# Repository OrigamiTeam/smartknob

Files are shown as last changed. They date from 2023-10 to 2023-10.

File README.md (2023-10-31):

# ⚠️⚠️⚠️ IBOM is not updated for my variant of the PCB, don't order blindly ⚠️⚠️⚠️

# SmartKnob
SmartKnob is an open-source input device with software-configurable endstops and virtual detents.

A brushless gimbal motor is paired with a magnetic encoder to provide closed-loop torque feedback control, making it
possible to dynamically create and adjust the feel of detents and endstops.

Join the [Discord community](https://discord.gg/5jyhjcbTnR) to discuss the project with others, show off your build, or help answer each others' questions!




# Designs

## SmartKnob View
The "SmartKnob View" is the premium SmartKnob experience with an integrated display shown in my [demo video](https://www.youtube.com/watch?v=ip641WmY4pA). Under active development.

🎉 **Motors are [now available](https://www.sparkfun.com/products/20441)!** If you've been following this project,
you'll know that the recommended motors went out of stock nearly immediately after it was published.
Thanks to [the community](https://github.com/scottbez1/smartknob/issues/16#issuecomment-1094482805%5D), we were able to
identify the likely original manufacturer, and recently SparkFun Electronics has been getting them produced and regularly
[stocking them](https://www.sparkfun.com/products/20441)! (However, they've been selling out quickly each time they restock, so definitely sign up for backorder notifications if they're out of stock when you check). Thanks to everyone who helped search and investigate different
motor options along the way!

Features:
 - 240x240 round LCD ("GC9A01"), protected by 39.5mm watch glass on rotor
 - BLDC gimbal motor, with a hollow shaft for mechanically & electrically connecting the LCD
 - Powered by ESP32-PICO-V3-02 (Lilygo TMicro32 Plus module)
 - PCB flexure and SMD resistors used as strain gauges for press detection (haptic feedback provided via the motor)
 - 8 side-firing RGB LEDs (SK6812-SIDE-A) illuminate ring around the knob
 - USB-C (2.0) connector for 5V power and serial data/programming (CH340)
 - VEML7700 ambient light sensor for automatic backlight & LED intensity adjustment
 - Versatile back plate for mounting - use either 4x screws, or 2x 3M medium Command strips (with cutouts for accessing removal tabs after installation)
 - Front cover snaps on for easy access to the PCB

**Current status:** Not recommended for general use, but may be a fun project for an advanced electronics hobbyist.

### Demo video

<a href="https://www.youtube.com/watch?v=ip641WmY4pA">
    
</a>

### How it works
<a href="https://www.youtube.com/watch?v=Q76dMggUH1M">
    
</a>

### 3D CAD

Exploded view

Latest Fusion 360 Model: https://a360.co/3BzkU0n

### Build your own?

While this is a "DIY" open-source project, it is not yet a mature plug-and-play project. If you intend to build your own, note that it requires advanced soldering experience to build - very small-pitch surface-mount soldering is required (reflow or hot air recommended), and assembly is quite time-consuming and delicate. Please go into it with the expectation that you will almost certainly need to be able to troubleshoot some hardware and firmware issues yourself - I recommend reviewing/understanding the schematics and basic firmware before jumping in!

More documentation on the BOM and what parts you need to order is coming in the future - thanks so much for your interest! Follow me on [Twitter](https://twitter.com/scottbez1) for the latest updates on this and other projects.

View the latest auto-generated (untested) [Base PCB Interactive BOM](https://smartknob-artifacts.s3.us-west-1.amazonaws.com/master/electronics/view_base-ibom.html) and [Screen PCB Interactive BOM](https://smartknob-artifacts.s3.us-west-1.amazonaws.com/master/electronics/view_screen-ibom.html) (or, the combined [BOM csv](https://smartknob-artifacts.s3.us-west-1.amazonaws.com/master/electronics/view_base-bom.csv)) for electronics/hardware parts list. ⚠️ These are auto-generated from the latest untested revision on GitHub. For tested/stable/recommended artifacts, use a [release](https://github.com/scottbez1/smartknob/releases) instead.

A few miscellaneous notes in the meantime:

 - There's limited space inside the LCD mount for wiring, and 8 wires need to fit through the hole in the center. I used 30 AWG wire-wrapping wire. Enamel-coated wire would probably work too.
 - Older versions of the design (as seen in the videos) used glued-on BF350-3AA strain gauges to detect presses; in v0.5 these were replaced with footprints for SMD resistors, which exhibit similar properties when stretched/compressed and are much easier to assemble. 
 - The TMC6300 is _tiny_ and has a bottom pad, so I would seriously consider getting a stencil along with the PCB order. Even with the stencil I needed to manually clean up some bridging afterward; I _highly_ recommend Chip Quik NC191 gel flux, available on [Amazon](https://amzn.to/3MGDSr5) (or use this [non-affiliate link](https://www.amazon.com/Smooth-Flow-No-Clean-syringe-plunger/dp/B08KJPG3NZ) instead) or from your electronics distributor of choice. Flux is also very helpful when soldering the LCD ribbon cable to to screen PCB.
 - For breadboard prototyping, the [TMC6300-BOB](https://www.trinamic.com/support/eval-kits/details/tmc6300-bob/) or SparkFun's [TMC6300 driver board](https://www.sparkfun.com/products/21867) are awesome and way easier to work with than the bare chip if you just want to play around with low current BLDC motors
 - For AliExpress purchases: I highly recommend **only** using AliExpress Standard Shipping (purchasing in the US). I have had multiple purchases take months or never get delivered when purchased with Cainiao or other low cost shipping options, whereas AliExpress Standard is very reliable and generally faster in my experience.
 - Make sure to check the [open issues](https://github.com/scottbez1/smartknob/issues) - this design is not yet "stable", so beware that everything may not go smoothly.

Future plans:
 - consider switch to using an ESP32-S3-MINI-1 module
 - get wifi configured and working (probably MQTT?). Currently memory is an issue with the full display framebuffer sprite. PSRAM might fix this (requires newer ESP-IDF & unreleased Arduino core, and from a brief test I got horrible performance with PSRAM enabled), or the next item might help reduce memory:
 - migrate to LVGL, for better display rendering and easy support for menus, etc. Shouldn't require a full 240x240x24b framebuffer in memory, freeing some for wifi, etc.
 - Home Assistant integration, or other real-world applications
 - ???
 - [Profit](https://github.com/sponsors/scottbez1/) 😉

 #### Already built one?
Check out the [firmware/software documentation](https://paper.dropbox.com/doc/SmartKnob-firmware-and-software--B_oWj~L1dXqHgAqqYmhwwuqzAg-VUb9nq7btuhnHw5KlgJIH)
for tips on getting it programmed and hooking it up to your own software integrations.

If you've already uploaded the standard firmware and gone through the calibration process (see guide linked above if you don't know what this means),
go to https://scottbez1.github.io/smartknob/ to try out an interactive web-based demo that uses Web Serial to talk to a SmartKnob that's plugged into your
computer's USB port!

#### Base PCB

<a href="https://smartknob-artifacts.s3.us-west-1.amazonaws.com/master/electronics/view_base-front-3d.png">
    
</a>
<a href="https://smartknob-artifacts.s3.us-west-1.amazonaws.com/master/electronics/view_base-back-3d.png">
    
</a>

Ordering notes: use white soldermask, for reflecting light from RGB LED ring around the knob. Should be 1.2mm thick (not "standard" 1.6mm).

If you are ordering a stencil for solder paste from JLCPCB and plan to apply paste by hand (as
[shown in the video](https://youtu.be/Q76dMggUH1M?t=372)) without a stencil frame/machine, make sure to select
**"Customized size"** and enter smaller dimensions (e.g. 100mm x 100mm) to avoid getting a much larger stencil than you
need. This will also likely reduce the cost of shipping substantially! Also, select only the **Top** side; the bottom
only has 2 SMT components - the motor connector and VEML7700 ALS - so it's not worth getting a stencil for that.

Latest auto-generated (untested and likely broken!) artifacts⚠️:

[Schematic](https://smartknob-artifacts.s3.us-west-1.amazonaws.com/master/electronics/view_base-schematic.pdf)

[Interactive BOM](https://smartknob-artifacts.s3.us-west-1.amazonaws.com/master/electronics/view_base-ibom.html)

[PCB Packet](https://smartknob-artifacts.s3.us-west-1.amazonaws.com/master/electronics/view_base-pcb-packet.pdf)

[Gerbers](https://smartknob-artifacts.s3.us-west-1.amazonaws.com/master/electronics/view_base-jlc/gerbers.zip)

⚠️ For tested/stable/recommended artifacts, use a [release](https://github.com/scottbez1/smartknob/releases) instead.

#### Screen PCB

<a href="https://smartknob-artifacts.s3.us-west-1.amazonaws.com/master/electronics/view_screen-front-3d.png">
    
</a>
<a href="https://smartknob-artifacts.s3.us-west-1.amazonaws.com/master/electronics/view_screen-back-3d.png">
    
</a>

Ordering notes: Must be 1.2mm thick (not "standard" 1.6mm) per mechanical design. (The PCB silkscreen mentions 0.6mm thickness - this is the thickness of the **VHB tape** for adhering the LCD; the PCB should be 1.2mm thick)

There are few enough components on the Screen PCB that I chose to hand-solder them rather than reflow with solder paste
and a stencil, but if you order a stencil, see the note above about selecting a "Customized size" to be easier to
handle and save on shipping. Also make sure to select the **Bottom** side only; all the components are on the bottom
side of the screen PCB.

Latest auto-generated (untested and likely broken!) artifacts⚠️:

[Schematic](https://smartknob-artifacts.s3.us-west-1.amazonaws.com/master/electronics/view_screen-schematic.pdf)

[Interactive BOM](https://smartknob-artifacts.s3.us-west-1.amazonaws.com/master/electronics/view_screen-ibom.html)

[PCB Packet](https://smartknob-artifacts.s3.us-west-1.amazonaws.com/master/electronics/view_screen-pcb-packet.pdf)

[Gerbers](https://smartknob-artifacts.s3.us-west-1.amazonaws.com/master/electronics/view_screen-jlc/gerbers.zip)

⚠️ For tested/stable/recommended artifacts, use a [release](https://github.com/scottbez1/smartknob/releases) instead.

#### Printed parts
You will need six printed parts. The current stable designs can be found as STL assets in the [v185 mechanical release](https://github.com/scottbez1/smartknob/releases/tag/releases%2Fmechanical%2Fv185-dummy-tag) or you can export the latest untested designs from the CAD model by opening it in Fusion 360: https://a360.co/3BzkU0n

The parts can _probably_ be FDM 3D printed with a well-tuned printer, but the parts shown in videos/photos were MJF printed in nylon for tight tolerances and better surface finish. 

If you wanted a simpler build, you could omit the LCD and just merge the knob + glass from the model into a single STL to get a closed-top knob.

Export and print the following 6 parts:
* `Enclosure`
* `Knob` (RotorAssembly->KnobAssembly->Knob)
* `ScreenPlatform`
* `RotorSpacer` (RotorAssembly->RotorSpacer)
* `MountBase`
* `BackPlate`

⚠️ If you opt to go for MJF Nylon printing from JLCPCB, their system may complain about `< 0.8mm wall thickness detected` on the `MountBase`, `ScreenPlatform` and `RotorSpacer` parts. This appears to be a false positive, possibly on some of the print tapers. You should be able to ignore this, as all print orders at JLCPCB are subject to a final manual review, and they will contact you by email if there are any job-stopping issues or risks with your prints.

## NanoFOC (3rd party)
If you're looking to tinker with FOC/haptic feedback, but don't want to build a full SmartKnob View yourself, I can
recommend the NanoFOC DevKit++, an [open-source design](https://github.com/katbinaris/nanofoc_devkit) made and
[sold](https://store.binaris.io/products/nanofoc-devkit) by a member of the SmartKnob community! It's super compact
and is a great testbed or core for building your own BLDC-based haptic input device.

Image of the NanoFOC PCB

The NanoFOC uses an ESP32-S3, and the SmartKnob firmware works on it out of the box; just select the `nanofoc`
environment in PlatformIO rather than the `view` environment when uploading.

# Frequently Asked Questions (FAQ)

### Can I use this cheap gimbal BLDC motor I found on AliExpress?

I can't stop you, but I will caution that **you probably won't be super happy with it** depending on your intended application.

Nearly every off-the-shelf BLDC gimbal motor that the community has tested (which is pretty much ALL the cheap ones you'll find on AliExpress, trust me) has
_moderate to severge cogging_. That means the motor wants to snap to certain positions by itself even when unpowered. This means you won't be able to get
completely smooth rotation when virtual detents are turned off, and the motor's cogging may interfere with or overpower the virtual detents, particularly if
you set them to lower strength or make then very fine-grained.

The recommended motor is definitely the best (i.e. lowest cogging) off-the-shelf motor we've come across so far, and is the only readily-available motor
that I would consider "good" for this application.

If you've found another motor that is completely smooth when unpowered, we'd LOVE to hear about it in the discord; if you're wondering about some cheap motor
you saw online, either just order one and try it for yourself, or ask about it in discord but don't be surprised (or offended) if the response you get is
something terse like "nope, no good".

### How much does it cost?

I wish I could tell you now, but I don't actually know off the top of my head. Check back soon - I've only built a few so far, which was the result of a bunch of tinkering and prototyping over an extended period, so I don't have all the expenses tallied up yet. Probably less than $200 in parts? But some items have gotten more expensive, and you may be limited by minimum order quantities or shipping charges from multiple separate suppliers.

### Does it work with XYZ?

Not yet, regardless of whatever "XYZ" you're thinking of. So far I've only implemented enough firmware for the demo shown in the video, so you can't actually use it for anything productive yet. The basic detent configuration API is there, but not much else. Lots of firmware work remains to be done. If you build one, I'd love your help adding support for "XYZ" though!

### Can I buy one as a kit or already assembled?

Probably not? Or at least, I don't have any immediate plans to sell them myself. It's not that I don't want you to be happy, but hardware is a hard business and I just work on this stuff in my free time.

It's open source with a fairly permissive license though, so in theory anyone could start offering kits/assemblies. If someone does go down that route of selling them, note that attribution is
 _required_ (and I wouldn't say no to [royalties/tips/thanks](https://github.com/sponsors/scottbez1/) if you're in a giving mood 🙂).

# Firmware and Software
More extensive documentation of the firmware and software (and how to get started) can be found in the dedicated [SmartKnob Firmware and Software Guide](https://paper.dropbox.com/doc/SmartKnob-firmware-and-software--Byho6npe9XvZLZLxJ_8bK5TqAg-VUb9nq7btuhnHw5KlgJIH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)

## General Component Info

### Magnetic encoders

#### MT6701 (MagnTek)
Excellent sensor at a reasonable price - highly recommended. Less noisy than TLV493D, and more responsive (control loop is more stable) using SSI.

 - Lots of IO options - SSI, I2C, and ABZ - should offer good response latency
 - SSI includes CRC to validate data
 - No power-down or low-power options - may not be ideal for battery-powered devices
 - Not available from US distributors (Mouser, Digi-Key)

[Datasheet](http://www.magntek.com.cn/upload/MT6701_Rev.1.5.pdf)

[Ordering (LCSC)](https://lcsc.com/product-detail/Angle-Linear-Position-Sensors_Magn-Tek-MT6701CT-STD_C2856764.html)

#### TLV493D (Infineon)
Not used in the SmartKnob view, but a common/popular magnetic encoder in general. It's a mediocre choice for a haptic feedback implementation. Easy to prototype with using [Adafruit's QWIIC breakout board](https://www.adafruit.com/product/4366).

In my testing, it's noisy, requiring filtering/smoothing that can slow responsiveness, hurting control loop stability. Or, with less filtering, the noise
can easily be "amplified" by the derivative component in the PID motor torque controller, causing audible (and tactile) humming/buzzing.

But the bigger issue is that there is apparently a known silicon issue that causes the internal ADC to sometimes completely lock up, requiring a full reset and re-configuration, which can cause delays/gaps in data! See section
5.6 in the [User Manual](https://www.infineon.com/dgdl/Infineon-TLV493D-A1B6_3DMagnetic-UM-v01_03-EN.pdf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)

    In the Master Controlled Mode (MCM) or the Fast Mode (FM) the ADC conversion may hang up. A hang up can
    be detected by:
     - Frame Counter (FRM) counter stucks and does not increment anymore.

In my experience testing 4 different Adafruit breakout boards, 2 of them (50%) regularly exhibit this lockup behavior within a minute or two of use. It is possible to detect and auto-reset (and there is code in the project to do so), but it is slow and may cause undesirable jumps/delays if the sensor locks up often.

[Datasheet](https://www.mouser.com/datasheet/2/196/Infineon_TLV493D_A1B6_DataSheet_v01_10_EN-1227967.pdf)

#### AS5600 (AMS)
A mediocre choice. Cheap breakout boards are readily available.

In my testing, it's fairly noisy (anecdotally, noisier than the TLV493d), requiring filtering/smoothing that can slow responsiveness, hurting control loop stability. Additionally, it saturates at a lower magnetic field strength than other sensors I tested, requiring a significant air gap (8-10mm) when used with a strong neodymium diametric magnet like [Radial Magnets 8995](https://www.digikey.com/en/products/detail/radial-magnets-inc/8995/5126077).

[Datasheet](https://ams.com/documents/20143/36005/AS5600_DS000365_5-00.pdf)

### Motor drivers
#### TMC6300-LA
This is a relatively new IC and it's a perfect match! There generally aren't any other drivers (with integrated fets) that meet the requirements for the low-voltage and low-current motors used in this project (DRV8316 might work, but has not been tested).

Highlights:
 - 2-11V DC motor supply input
 - Up to 1.2A RMS
 - Tiny (3x3mm QFN)

 [Datasheet](https://www.trinamic.com/fileadmin/assets/Products/ICs_Documents/TMC6300_datasheet_rev1.07.pdf)

 [Product page](https://www.trinamic.com/products/integrated-circuits/details/tmc6300-la/)

### Motors
#### 32mm Rotor, Hollow Shaft, Diametric magnet



- 32mm rotor
- 15mm overall height (including magnet), 12.75mm height w/o magnet, 9mm rotor height
- low/zero cogging - excellent for completely smooth input
- 5.9mm hollow shaft
- built-in diametric magnet for encoder
- Proven option

This is overall the easiest motor to get started with. Low cogging and a built-in diametric magnet are great!

Available [from SparkFun](https://www.sparkfun.com/products/20441)!

# Acknowledgements
This project was greatly inspired by Jesse Schoch's video "[haptic textures and virtual detents](https://www.youtube.com/watch?v=1gPQfDkX3BU)" and the
corresponding [discussion in the SimpleFOC community](https://community.simplefoc.com/t/haptic-textures/301). Seriously, this project wouldn't exist if not for that video - thank you Jesse!

# License

This project is licensed under Apache v2 (software, electronics, documentation) and Creative Commons Attribution 4.0 (hardware/mechanical) (see [LICENSE.txt](LICENSE.txt) and [Creative Commons](https://creativecommons.org/licenses/by/4.0/)).

    Copyright 2022 Scott Bezek
    
    Licensed under the Apache License, Version 2.0 (the "License");
    you may not use this file except in compliance with the License.
    You may obtain a copy of the License at
    
        http://www.apache.org/licenses/LICENSE-2.0
    
    Unless required by applicable law or agreed to in writing, software
    distributed under the License is distributed on an "AS IS" BASIS,
    WITHOUT WARRANTIES OR CONDITIONS OF ANY KIND, either express or implied.
    See the License for the specific language governing permissions and
    limitations under the License.

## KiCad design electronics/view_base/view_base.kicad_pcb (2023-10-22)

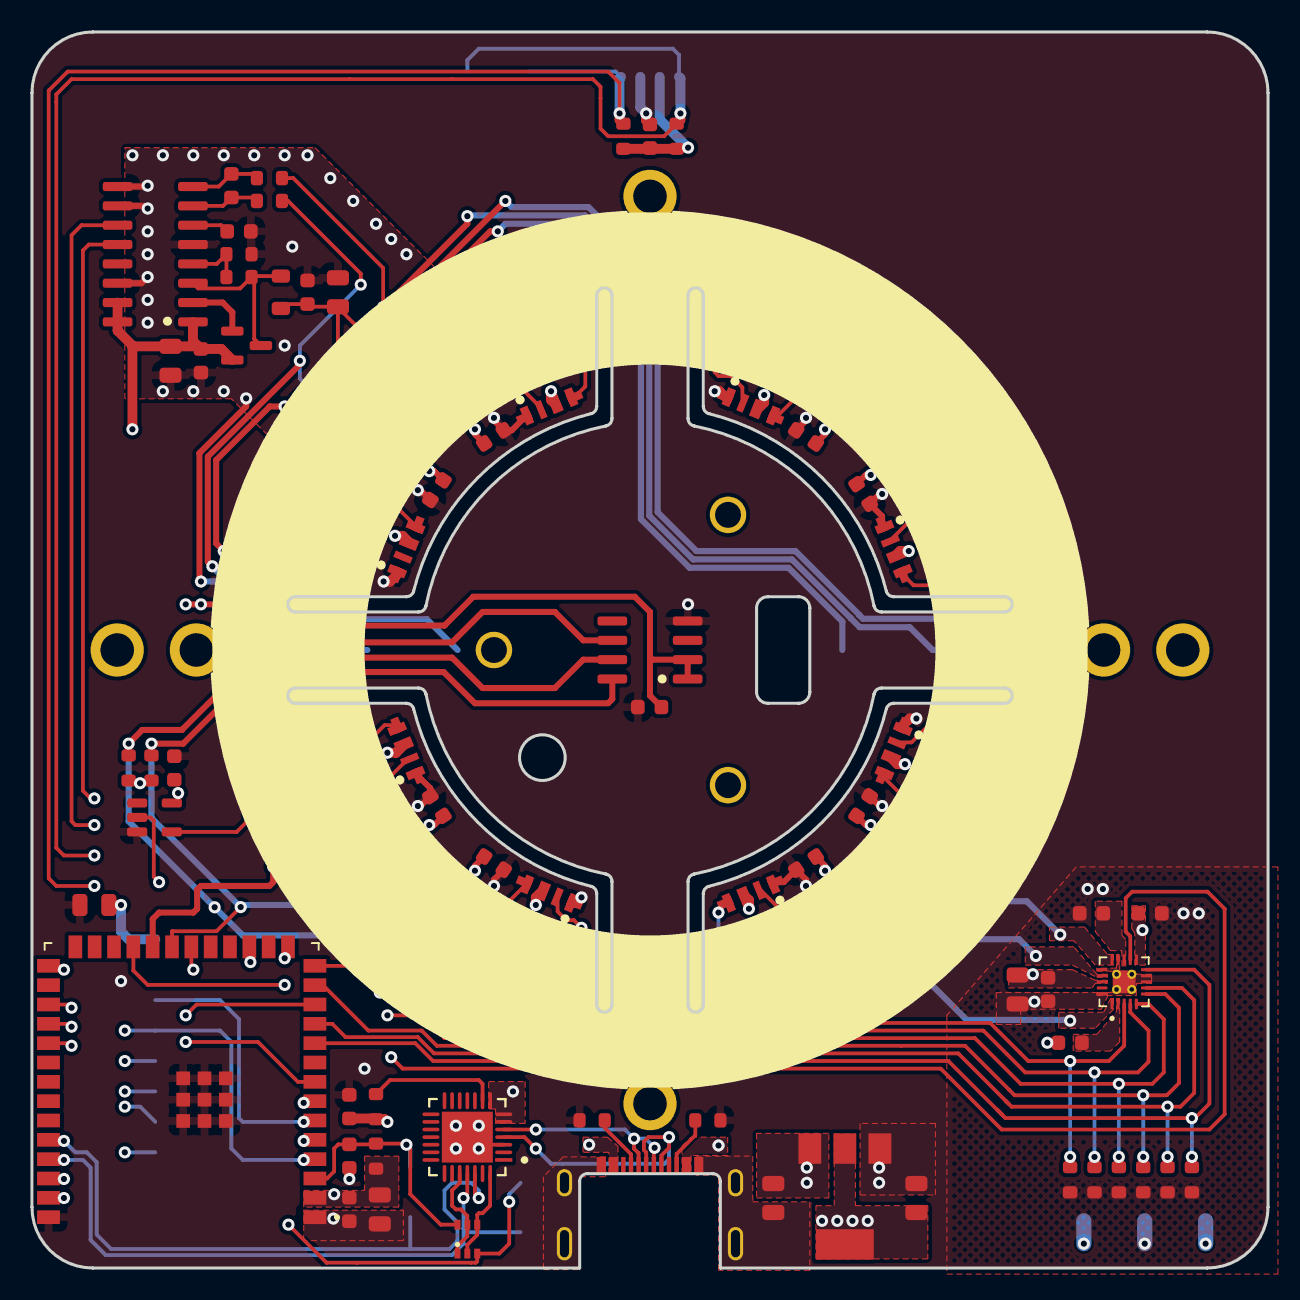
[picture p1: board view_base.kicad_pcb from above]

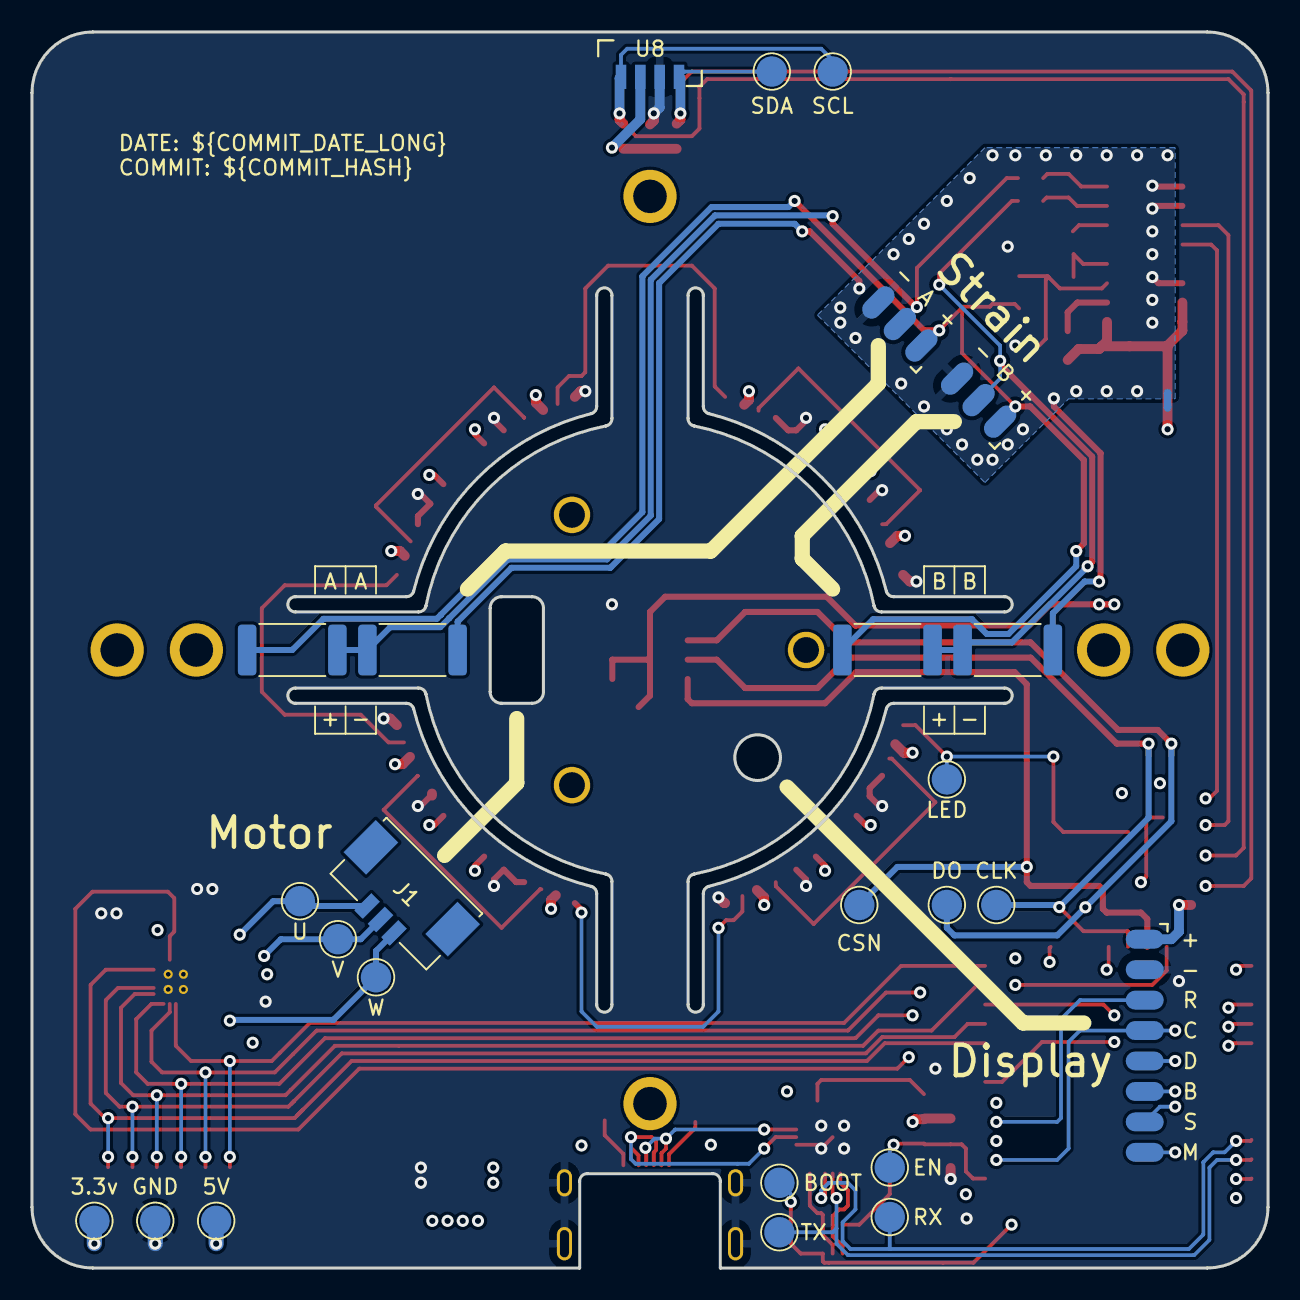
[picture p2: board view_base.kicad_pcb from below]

Board: 4 copper layers, 81.2 x 81.2 mm, 107 parts (26 on the bottom side), 58 nets.

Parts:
C1, C2, C3, C4, C5, C6, C7, C8, C11, C12, C14, C15, C17, C19, C20, C21, C22, C23, C25, C27, C29: 0.1uF; C_0603_1608Metric
C9, C10, C16, C18, C24, C26: 10uF; C_0805_2012Metric
C13: 22uF; C_0805_2012Metric
C28: 1uF; C_0603_1608Metric
D1, D2, D3, D4, D5, D6, D7, D8: SK6812SIDE-A; SK6812-SIDE-A
H1, H2, H3: MotorHole; MountingHole_M1.6
H4, H5, H6, H7: MountHole; MountingHole_2.2mm_M2_ISO7380_Pad_NonVirtual
H8, H9: AlignmentHole; MountingHole_2.2mm_M2_ISO7380_Pad_NonVirtual
J1: BLDC; 532610371
J2: USB_C_Receptacle_USB2.0; USB4510_NoPaste
J3: LCD; SolderPads_2mm_8
J4: A; SolderPads_2mm_3_STRAIN
J5: B; SolderPads_2mm_3_STRAIN
L1: 3.3uH; L_0805_2012Metric
NT1: NetTie_2; NetTie-2_SMD_Pad0.5mm
Q1: MMBT4403; SOT-23
Q2: UMH3N; SOT-363_SC-70-6
R1, R2: 5.1k; R_0603_1608Metric
R3, R7, R8, R9, R10, R11, R12, R17: 10k; R_0603_1608Metric
R4: 8.2k; R_0603_1608Metric
R5, R6: 100; R_0603_1608Metric
R13, R14, R15, R16: 2.2k; R_0603_1608Metric
R18, R19, R20, R21: 330; R_2512_6332Metric
R22: 1K; R_0603_1608Metric
TP1: 5V; TestPoint_Pad_D2.0mm_ValueSilk
TP2: 3.3v; TestPoint_Pad_D2.0mm_ValueSilk
TP3: GND; TestPoint_Pad_D2.0mm_ValueSilk
TP4: SDA; TestPoint_Pad_D2.0mm_ValueSilk
TP5: SCL; TestPoint_Pad_D2.0mm_ValueSilk
TP6: U; TestPoint_Pad_D2.0mm_ValueSilk
TP7: V; TestPoint_Pad_D2.0mm_ValueSilk
TP8: W; TestPoint_Pad_D2.0mm_ValueSilk
TP9: CSN; TestPoint_Pad_D2.0mm_ValueSilk
TP10: CLK; TestPoint_Pad_D2.0mm_ValueSilk
TP11: DO; TestPoint_Pad_D2.0mm_ValueSilk
TP12: LED; TestPoint_Pad_D2.0mm_ValueSilk
TP13: EN; TestPoint_Pad_D2.0mm_ValueSilk
TP14: BOOT; TestPoint_Pad_D2.0mm_ValueSilk
TP15: TX; TestPoint_Pad_D2.0mm_ValueSilk
TP16: RX; TestPoint_Pad_D2.0mm_ValueSilk
U1: MT6701-CT; SOIC-8_3.9x4.9mm_P1.27mm
U2: CP2102N-A02-GQFN28; Silicon_Labs-CP2102N-A02-GQFN28-IPC_A
U4: HX711; SOIC-16_3.9x9.9mm_P1.27mm
U5: TMC6300; QFN-20-1EP_3x3mm_P0.4mm_EP1.65x1.65mm_ThermalVias_LargerVia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
U7: SN74LV1T34DBV; SOT-23-5
U8: VEML7700; VEML7700-TOP
U9: TS1117BCW33_RPG; SOT-223-3_TabPin2_GndOutIn
U10: ESP32-S3-WROOM-1-N8R8; XCVR_ESP32S3WROOM1N8R8U
Z5: dummy_keepouts; ViewKeepouts3d
Z6, Z7, Z8: RotorScrew (BOM-only); bom_only_no_pin
Z9: WatchGlass39.5mm; bom_only_no_pin
Z10: BLDCMotor; bom_only_no_pin

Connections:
+3V3: C10.1, C11.1, C12.1, C16.1, C17.1, C20.1, C24.1, C25.1, C26.1, C27.1, J3.1, Q1.2 (E), R13.1, R14.1, R15.1, R16.2, R17.1, R22.1, TP2.1, U1.1 (VDD), U1.2 (MODE), U2.6 (VDD), U2.7 (VREGIN), U2.8 (VBUS), U4.1 (VSUP), U4.15 (RATE), U4.16 (DVDD), U5.11 (VIO/~STDBY), U8.2 (VDD), U9.2 (Output), U10.2 (3V3)
+5V: C1.1, C2.1, C3.1, C4.1, C5.1, C6.1, C7.1, C8.1, C9.1, C13.1, C14.1, C15.1, C29.1, D1.2 (VDD), D2.2 (VDD), D3.2 (VDD), D4.2 (VDD), D5.2 (VDD), D6.2 (VDD), D7.2 (VDD), D8.2 (VDD), J2.A4 (VBUS), J2.A9 (VBUS), J2.B4 (VBUS), J2.B9 (VBUS), TP1.1, U5.18 (VS), U7.5 (VCC), U9.3 (Input)
/DTR: Q2.2 (B1), Q2.4 (E2), U2.28 (DTR)
/ESP32_BOOT: Q2.3 (C2), TP14.1, U10.27 (IO0)
/ESP32_EN: C28.1, Q2.6 (C1), R17.2, TP13.1, U10.3 (EN)
/LCD_BACKLIGHT: J3.6, U10.5 (IO5)
/LCD_CMD: J3.8, U10.38 (IO2)
/LCD_CS: J3.7, U10.17 (IO9)
/LCD_DATA: J3.5, U10.15 (IO3)
/LCD_RST: J3.3, U10.6 (IO6)
/LCD_SCK: J3.4, U10.4 (IO4)
/LED_DATA_3V3: U7.2 (A), U10.7 (IO7)
/LED_DATA_5V: D1.1 (DIN), TP12.1, U7.4 (Y)
/MAG_CLK: R16.1, TP10.1, U1.7 (B/V/SCL/CLK), U10.21 (IO13)
/MAG_CSN: TP9.1, U1.8 (Z/W/CSN), U10.22 (IO14)
/MAG_DO: R15.2, TP11.1, U1.6 (A/U/SDA/DO), U10.30 (IO37)
/RTS: Q2.1 (E1), Q2.5 (B2), U2.24 (RTS)
/SCL: R14.2, TP5.1, U8.1 (SCL), U10.12 (IO8)
/SDA: R13.2, TP4.1, U8.4 (SDA), U10.8 (IO15)
/STRAIN_DO: U4.12 (DOUT), U10.31 (IO38)
/STRAIN_E+: C18.1, C19.1, J4.1, J5.1, L1.2, R18.1, R20.2
/STRAIN_S+: J4.2, R6.1, R18.2, R19.1
/STRAIN_S-: J5.2, R5.2, R20.1, R21.2
/STRAIN_SCK: U4.11 (PD_SCK), U10.39 (IO1)
/TMC_DIAG: U5.12 (DIAG), U10.29 (IO36)
/TMC_UH: R7.1, U5.3 (UH), U10.14 (IO20)
/TMC_UL: R10.1, U5.6 (UL), U10.13 (IO19)
/TMC_VH: R8.1, U5.4 (VH), U10.23 (IO21)
/TMC_VL: R12.1, U5.10 (VL), U10.10 (IO17)
/TMC_WH: R9.1, U5.5 (WH), U10.20 (IO12)
/TMC_WL: R11.1, U5.7 (WL), U10.11 (IO18)
/USB_CC1: J2.A5 (CC1), R1.1
/USB_CC2: J2.B5 (CC2), R2.1
/USB_D+: J2.A6 (D+), J2.B6 (D+), U2.4 (D+)
/USB_D-: J2.A7 (D-), J2.B7 (D-), U2.5 (D-)
/USB_SERIAL_RXI: TP15.1, U2.25 (RXD), U10.37 (TXD0)
/USB_SERIAL_TXO: TP16.1, U2.26 (TXD), U10.36 (RXD0)
GND: C1.2, C2.2, C3.2, C4.2, C5.2, C6.2, C7.2, C8.2, C9.2, C10.2, C11.2, C13.2, C14.2, C17.2, C20.2, C21.2, C24.2, C25.2, C26.2, C27.2, C28.2, C29.2, D1.4 (VSS), D2.4 (VSS), D3.4 (VSS), D4.4 (VSS), D5.4 (VSS), D6.4 (VSS), D7.4 (VSS), D8.4 (VSS), J2.A1 (GND), J2.A12 (GND), J2.B1 (GND), J2.B12 (GND), J2.S1 (SHIELD), J3.2, NT1.2, R1.2, R2.2, R7.2, R8.2, R9.2, R10.2, R11.2, R12.2, TP3.1, U1.4 (GND), U2.3 (GND), U2.29 (GND), U5.8 (GND), U5.9 (GND), U5.14 (GND), U5.16 (BRUV), U5.20 (BRW), U5.PAD, U7.3 (GND), U8.3 (GND), U9.1 (GND), U10.1 (GND), U10.40 (GND), U10.41_1 (GND), U10.41_2 (GND), U10.41_3 (GND), U10.41_4 (GND), U10.41_5 (GND), U10.41_6 (GND), U10.41_7 (GND), U10.41_8 (GND), U10.41_9 (GND)
GNDA: C12.2, C16.2, C18.2, C19.2, C22.1, J4.3, J5.3, NT1.1, R4.2, R19.2, R21.1, U4.5 (AGND), U4.9 (INB-), U4.10 (INB+), U4.14 (XI)
unnamed: D1.3 (DOUT), D2.1 (DIN)
unnamed: D2.3 (DOUT), D3.1 (DIN)
unnamed: D3.3 (DOUT), D4.1 (DIN)
unnamed: D4.3 (DOUT), D5.1 (DIN)
unnamed: D5.3 (DOUT), D6.1 (DIN)
unnamed: D6.3 (DOUT), D7.1 (DIN)
unnamed: D7.3 (DOUT), D8.1 (DIN)
unnamed: J1.1, TP8.1, U5.1 (W)
unnamed: J1.2, TP7.1, U5.17 (V)
unnamed: J1.3, TP6.1, U5.15 (U)
unnamed: Q1.1 (B), U4.2 (BASE)
unnamed: L1.1, Q1.3 (C), R3.1, U4.3 (AVDD)
unnamed: R22.2, U2.9 (~RST)
unnamed: C23.1, R6.2, U4.8 (INA+)
unnamed: C23.2, R5.1, U4.7 (INA-)
unnamed: C22.2, U4.6 (VBG)
unnamed: R3.2, R4.1, U4.4 (VFB)
unnamed: C21.1, U5.13 (1V8OUT)
unnamed: C15.2, U5.2 (VCP)

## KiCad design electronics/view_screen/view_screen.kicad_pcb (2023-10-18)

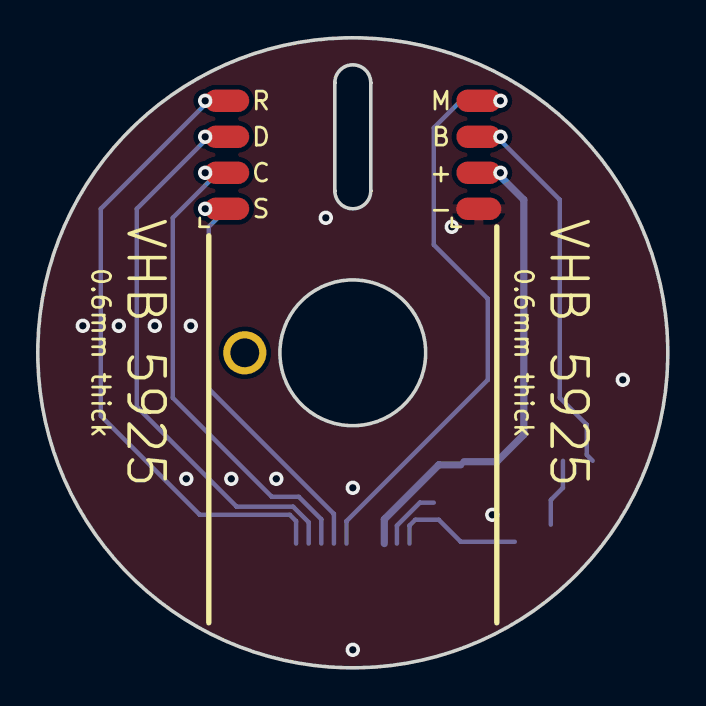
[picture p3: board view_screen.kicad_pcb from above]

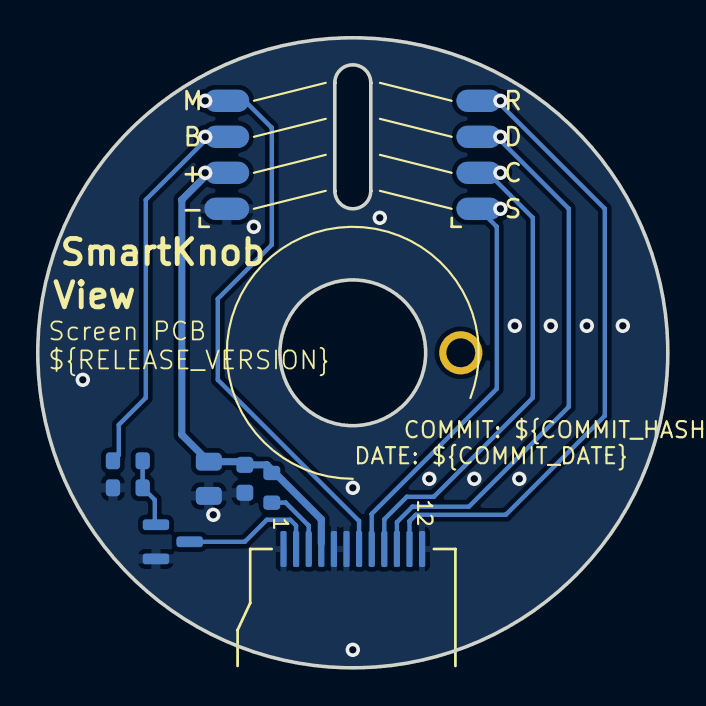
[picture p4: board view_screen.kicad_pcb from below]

Board: 2 copper layers, 35.0 x 35.0 mm, 12 parts (9 on the bottom side), 11 nets.

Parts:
C1: 22uF; C_0805_2012Metric
C2: 0.1uF; C_0603_1608Metric
H1: AlignmentHole; AlignmentHole_1.6
J1, J3, J4, J5: Conn_01x04; SolderPads_2mm_4
J2: GC9A01; GC9A01Round1.28
Q1: 2N7002; SOT-23
R1: 10k; R_0603_1608Metric
R2: 22R; R_0603_1608Metric
R3: 1M; R_0603_1608Metric

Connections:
/BACKLIGHT_EN: J1.3, J4.3, R1.1
/DC: J1.4, J2.7, J4.4
/LEDA: J2.3, R2.2
/LEDK: J2.2, Q1.3 (D)
/MOSI: J2.10, J3.3, J5.3
/SCK: J2.9, J3.2, J5.2
/VDD: C1.1, C2.1, J1.2, J2.4, J4.2, R2.1
/nCS: J2.8, J3.1, J5.1
/nRESET: J2.11, J3.4, J5.4
GND: C1.2, C2.2, J1.1, J2.1, J2.5, J2.6, J2.12, J4.1, Q1.2 (S), R3.2
unnamed: Q1.1 (G), R1.2, R3.1

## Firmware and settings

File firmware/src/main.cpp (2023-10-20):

#include <Arduino.h>

#include "configuration.h"
#include "display_task.h"
#include "interface_task.h"
#include "motor_task.h"

Configuration config;

#if SK_DISPLAY
static DisplayTask display_task(0);
static DisplayTask* display_task_p = &display_task;
#else
static DisplayTask* display_task_p = nullptr;
#endif
static MotorTask motor_task(1, config);


InterfaceTask interface_task(0, motor_task, display_task_p);

void setup() {
  #if SK_DISPLAY
  display_task.setLogger(&interface_task);
  display_task.begin();

  // // Connect display to motor_task's knob state feed
  motor_task.addListener(display_task.getKnobStateQueue());
  interface_task.begin();
  interface_task.setConfiguration(&config);

  #endif

  config.setLogger(&interface_task);
  bool isFFatOk = config.loadFromDisk();

  motor_task.setLogger(&interface_task);
  motor_task.begin();
  // motor_task.runCalibration();

// config.saveToDisk();

  // Free up the Arduino loop task
  vTaskDelete(NULL);
}

void loop() {
  char buf[50];
  static uint32_t last_stack_debug;
  if (millis() - last_stack_debug > 1000) {
    interface_task.log("Stack high water:");
    snprintf(buf, sizeof(buf), "  main: %d", uxTaskGetStackHighWaterMark(NULL));
    interface_task.log(buf);
    #if SK_DISPLAY
      snprintf(buf, sizeof(buf), "  display: %d", uxTaskGetStackHighWaterMark(display_task.getHandle()));
      interface_task.log(buf);
    #endif
    snprintf(buf, sizeof(buf), "  motor: %d", uxTaskGetStackHighWaterMark(motor_task.getHandle()));
    interface_task.log(buf);
    snprintf(buf, sizeof(buf), "  interface: %d", uxTaskGetStackHighWaterMark(interface_task.getHandle()));
    interface_task.log(buf);
    snprintf(buf, sizeof(buf), "Heap -- free: %d, largest: %d", heap_caps_get_free_size(MALLOC_CAP_8BIT), heap_caps_get_largest_free_block(MALLOC_CAP_8BIT));
    interface_task.log(buf);
    last_stack_debug = millis();
  }
}

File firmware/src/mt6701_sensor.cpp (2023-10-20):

#include "mt6701_sensor.h"
#include "driver/spi_master.h"

static const float ALPHA = 0.4;


static uint8_t tableCRC6[64] = {
 0x00, 0x03, 0x06, 0x05, 0x0C, 0x0F, 0x0A, 0x09,
 0x18, 0x1B, 0x1E, 0x1D, 0x14, 0x17, 0x12, 0x11,
 0x30, 0x33, 0x36, 0x35, 0x3C, 0x3F, 0x3A, 0x39,
 0x28, 0x2B, 0x2E, 0x2D, 0x24, 0x27, 0x22, 0x21,
 0x23, 0x20, 0x25, 0x26, 0x2F, 0x2C, 0x29, 0x2A,
 0x3B, 0x38, 0x3D, 0x3E, 0x37, 0x34, 0x31, 0x32,
 0x13, 0x10, 0x15, 0x16, 0x1F, 0x1C, 0x19, 0x1A,
 0x0B, 0x08, 0x0D, 0x0E, 0x07, 0x04, 0x01, 0x02
};

/*32-bit input data, right alignment, Calculation over 18 bits (mult. of 6) */
static uint8_t CRC6_43_18bit (uint32_t w_InputData)
{
 uint8_t b_Index = 0;
 uint8_t b_CRC = 0;

 b_Index = (uint8_t )(((uint32_t)w_InputData >> 12u) & 0x0000003Fu);

 b_CRC = (uint8_t )(((uint32_t)w_InputData >> 6u) & 0x0000003Fu);
 b_Index = b_CRC ^ tableCRC6[b_Index];

 b_CRC = (uint8_t )((uint32_t)w_InputData & 0x0000003Fu);
 b_Index = b_CRC ^ tableCRC6[b_Index];

 b_CRC = tableCRC6[b_Index];

 return b_CRC;
} 

#if SENSOR_MT6701

MT6701Sensor::MT6701Sensor() {}

void MT6701Sensor::init() {

    pinMode(PIN_MT_CSN, OUTPUT);
    digitalWrite(PIN_MT_CSN, HIGH);

  spi_bus_config_t tx_bus_config = {
      .mosi_io_num = -1,
      .miso_io_num = PIN_MT_DATA,
      .sclk_io_num = PIN_MT_CLOCK,
      .quadwp_io_num = -1,
      .quadhd_io_num = -1,
      .max_transfer_sz = 1000,
  };
  esp_err_t ret = spi_bus_initialize(SPI3_HOST, &tx_bus_config, SPI_DMA_CH_AUTO);
  ESP_ERROR_CHECK(ret);

  spi_device_interface_config_t tx_device_config = {
      .command_bits=0,
      .address_bits=0,
      .dummy_bits=0,
      .mode=1,
      .duty_cycle_pos=0,
      .cs_ena_pretrans=4,
      .cs_ena_posttrans=0,
      .clock_speed_hz=4000000,
      .input_delay_ns=0,
      .spics_io_num=PIN_MT_CSN,
      .flags = 0,
      .queue_size=1,
      .pre_cb=NULL,
      .post_cb=NULL,
  };
  ret=spi_bus_add_device(SPI3_HOST, &tx_device_config, &spi_device_);
  ESP_ERROR_CHECK(ret);


  spi_transaction_.flags = SPI_TRANS_USE_RXDATA;
  spi_transaction_.length = 24;
  spi_transaction_.rxlength = 24;
  spi_transaction_.tx_buffer = NULL;
  spi_transaction_.rx_buffer = NULL;
}

float MT6701Sensor::getSensorAngle() {
    uint32_t now = micros();
    if (now - last_update_ > 100) {
      
      esp_err_t ret=spi_device_polling_transmit(spi_device_, &spi_transaction_);
      assert(ret==ESP_OK);

      uint32_t spi_32 = (spi_transaction_.rx_data[0] << 16) | (spi_transaction_.rx_data[1] << 8) | spi_transaction_.rx_data[2];
      uint32_t angle_spi = spi_32 >> 10;

      uint8_t field_status = (spi_32 >> 6) & 0x3;
      uint8_t push_status = (spi_32 >> 8) & 0x1;
      uint8_t loss_status = (spi_32 >> 9) & 0x1;

      uint8_t received_crc = spi_32 & 0x3F;
      uint8_t calculated_crc = CRC6_43_18bit(spi_32 >> 6);
      
      if (received_crc == calculated_crc) {
        float new_angle = (float)angle_spi * 2 * PI / 16384;
        float new_x = cosf(new_angle);
        float new_y = sinf(new_angle);
        x_ = new_x * ALPHA + x_ * (1-ALPHA);
        y_ = new_y * ALPHA + y_ * (1-ALPHA);
      } else {
        error_ = {
          .error = true,
          .received_crc = received_crc,
          .calculated_crc = calculated_crc,
        };
      }

      last_update_ = now;
    }
    float rad = -atan2f(y_, x_);
    if (rad < 0) {
        rad += 2*PI;
    }
    return rad;
}

MT6701Error MT6701Sensor::getAndClearError() {
  MT6701Error out = error_;
  error_ = {};
  return out;
}

#endif

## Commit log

2023-10-07 Updated to esp32s3, cp2102, re-routed
    [view_base.kicad_pcb]
2023-10-18 refactored PCB
    [view_base.kicad_pcb, view_base.kicad_sch, view_screen.kicad_pcb]
2023-10-20 working screen, motor, magnet sensor
    [partitions-default-fat.csv]
2023-10-22 fixed strain sensor
    [view_base.kicad_pcb]

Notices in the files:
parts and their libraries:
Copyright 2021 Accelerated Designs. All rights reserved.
